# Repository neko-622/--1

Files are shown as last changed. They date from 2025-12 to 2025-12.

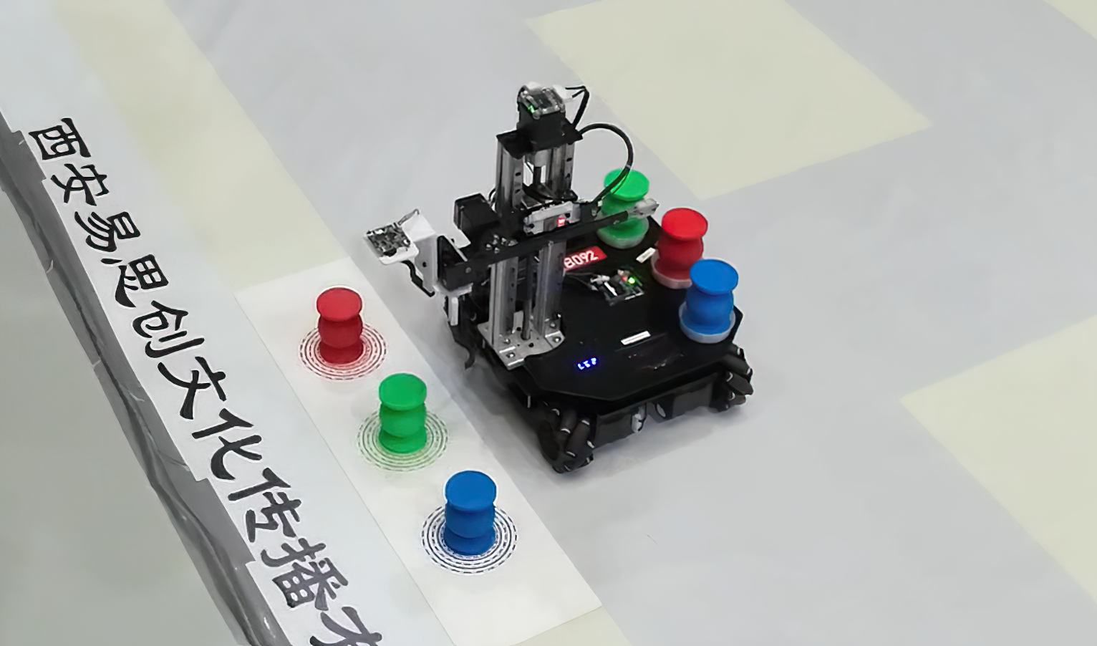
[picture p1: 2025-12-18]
2025智能物流项目简介_任务命题文档/IMG_8247.PNG

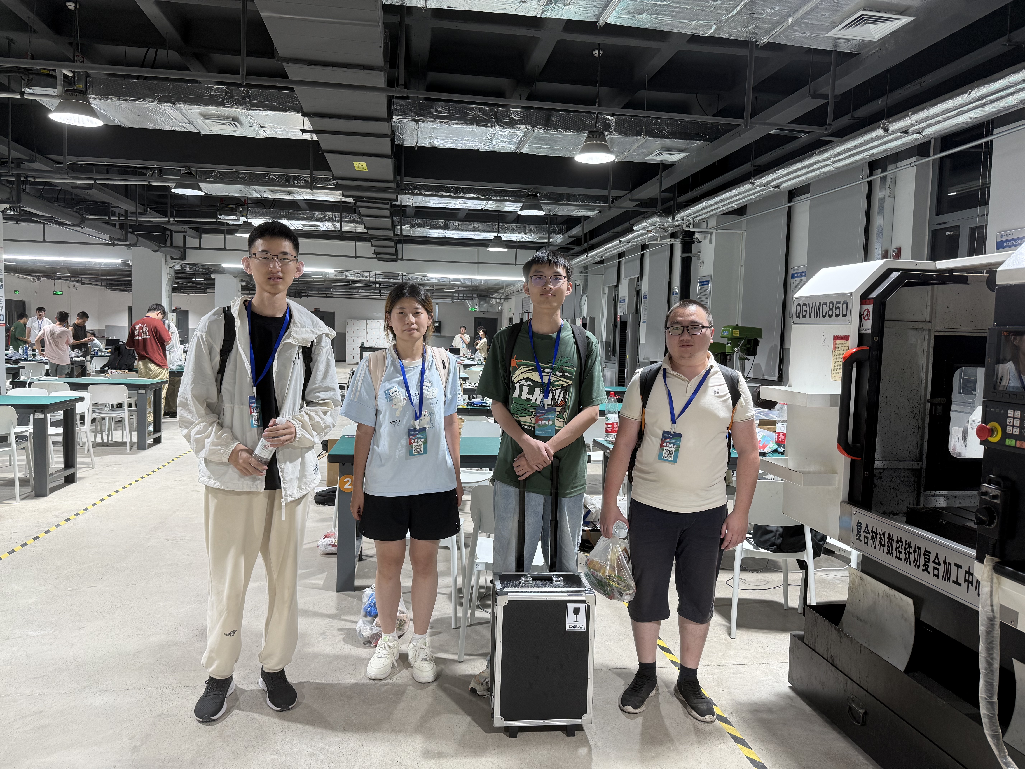
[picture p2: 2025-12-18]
2025智能物流项目简介_任务命题文档/IMG_8206.JPG

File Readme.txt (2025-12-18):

注意事项
1.PCB文件打板前请仔细检查所有封装，塔吊扩展板的降压模块可以自行替换。
2.视觉和电控代码都是经过实机测试的，不会有重大bug，但是注意电机模式和零位！
4.机械开源仅供参考，因为SW模型导出制图文件后又进行了少量的修改，整体没有大问题，但是细节需要自行打磨，打印件同理。
5.机械打板之前仔细检查孔位，可能有理线孔位置略有偏差，实物电机替换为DM4310，孔位和高度均不一致，根据实际需求修改。
6.机械打板推荐使用玻纤，因为绝缘。碳板导电。
7.注意硬件接线，注意电机零位，谨慎测试，注意安全！

2025年9月11日修改/勘误
1.共轴连接器购买链接错误，已经替换。

2025年9月18日提醒
1.PCB板中的降压模块由我们自行设计，封装如图箭头7，目前正在立创开源平台审核，我们自己是批量smt生产的，考虑到大家smt成本较高，建议大家使用其他商品降压模块进行替换，减小工作量且节约时间，后续将会上传替换降压模块的pcb版本。

2025年9月21日更新
1.前期提到的降压模块大家难以复刻的问题，已经上传修改了电源板和塔吊综合板降压模块的PCB文件。使用到的降压模块链接稍后更新到物料清单。再次提醒大家PCB打板之前细心检查，我们不对复刻过程中产生的任何损失负责。
2.在物料清单中更新了降压模块购买链接。
注意事项
1.电源板使用5V3A稳压输出模块，塔吊综合板的输出电压大家根据使用的舵机型号自定，模块输出电压可通过更换贴片电阻改变，详情询问客服。

2025年9月27日更新
1.整合了PCB文件，加入了
①降压模块
②新的2层主控板
③适配商品降压模块的电源板和塔吊综合板
2.在物料清单中更新了
①丝杆底部轴承型号
②原版低扭矩数字舵机（价格低但扭矩小）
③加入了铝型材购买时两端攻丝的提示

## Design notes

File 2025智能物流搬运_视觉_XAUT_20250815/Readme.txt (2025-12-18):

运行环境
开发板：Jetson Orin Nano 8GB
系统：SDK刷Jetson纯净系统（jetpack5.1.4）
环境：OpenCV

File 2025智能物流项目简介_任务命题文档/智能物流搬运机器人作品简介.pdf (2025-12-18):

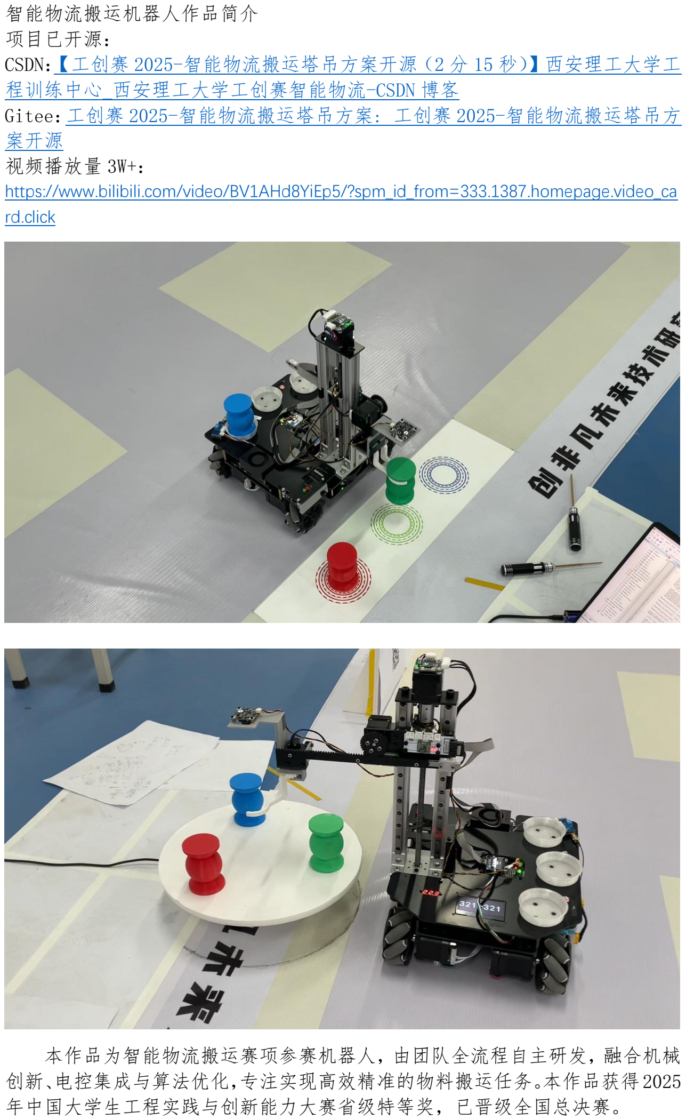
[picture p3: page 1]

智能物流搬运机器人作品简介
项目已开源：
CSDN：【工创赛 2025-智能物流搬运塔吊方案开源（2 分 15 秒）】西安理工大学工 程训练中心_西安理工大学工创赛智能物流-CSDN 博客 (https://blog.csdn.net/m0_74056439/article/details/150104661?spm=1001.2014.3001.5502)
Gitee：工创赛 2025-智能物流搬运塔吊方案: 工创赛 2025-智能物流搬运塔吊方 案开源 (https://gitee.com/pinksakura/Logistics_Vehicle_F407_V2)
视频播放量 3W+：
https://www.bilibili.com/video/BV1AHd8YiEp5/?spm_id_from=333.1387.homepage.video_ca rd.click (https://www.bilibili.com/video/BV1AHd8YiEp5/?spm_id_from=333.1387.homepage.video_card.click)

本作品为智能物流搬运赛项参赛机器人，由团队全流程自主研发，融合机械 创新、电控集成与算法优化，专注实现高效精准的物料搬运任务。本作品获得2025 年中国大学生工程实践与创新能力大赛省级特等奖，已晋级全国总决赛。

一、全自主设计与技术创新
整车机械、电控、视觉及硬件均自主开发，核心 PCB（主控 / 电源 / 拓展 / 塔吊转接）自主绘制打样，保障硬件系统的高集成与可靠性。机械 结构创新性采用 “塔吊”设计，灵活性大大提高。
搭载双重算法：视觉算法通过抗干扰优化，在强光干扰或目标部分遮挡 的情况下仍然可以准确识别目标；底盘定位结合麦克纳姆轮逆运动学解算， 配合视觉校正算法，实现 ±2mm 级精度，可精确按照预定轨迹运动，并无 误差返回出发点。
二、任务效率与功能突破
通过全流程时序优化，平均完赛时间控制在 2 分 15 秒内。支持 “一 键式” 自主运行，具备定位、二维码读取、多色物料跟踪抓取及色环 1 环 精度码垛等功能。
能源系统采用自主设计的锂电池组，满足全程能耗需求，支持实时电压 监测，支持电池热替换。
三、场景适配与工程价值
作品高集成、高稳定的特点，既满足赛事技术要求，也贴近智能制造对 物流自动化的实际需求，展现从实验室到工业应用的转化潜力。 团队以 “自主创新 + 工程落地” 为目标，通过全自主设计制作，以 敢于直面困难的精神，在赛事中呈现当代大学生的创新素养。

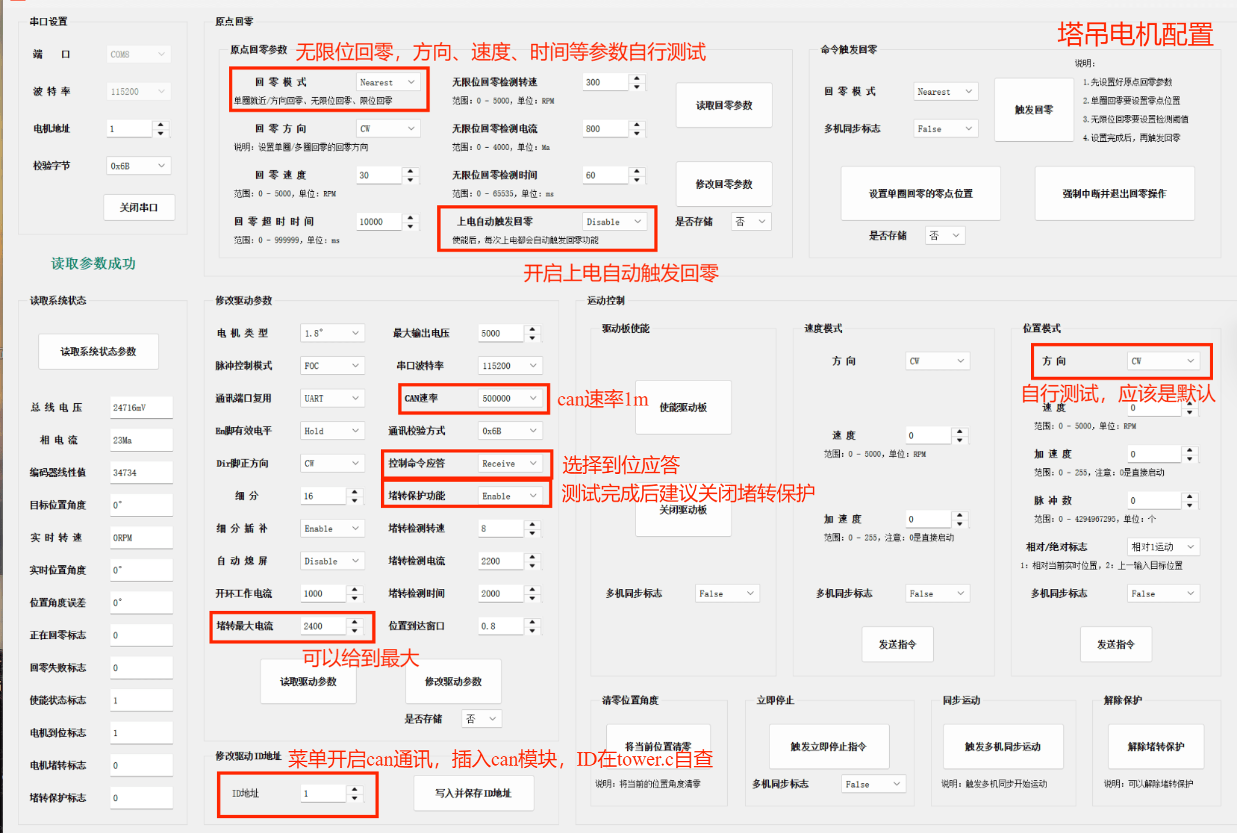
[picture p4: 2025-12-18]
附加资料及参数/塔吊张大头参数.png

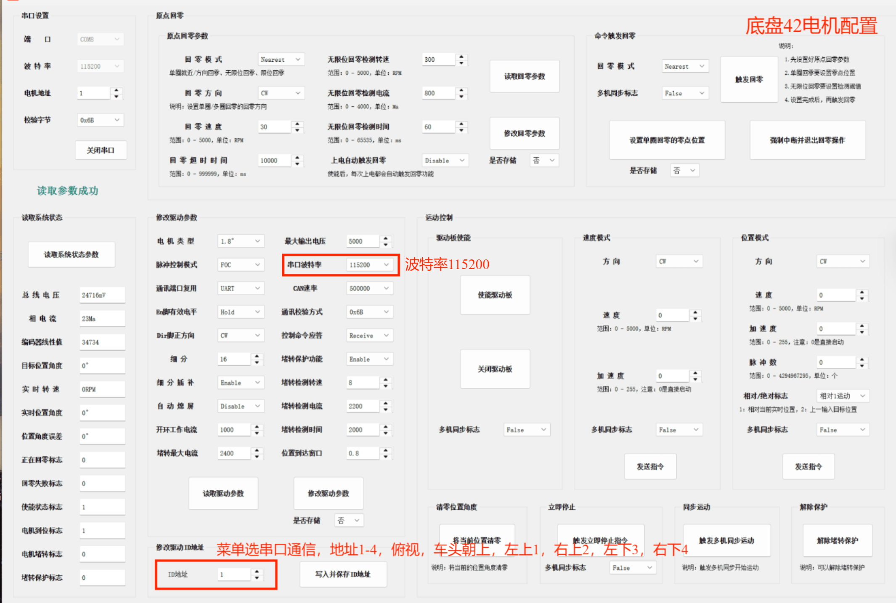
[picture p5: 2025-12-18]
附加资料及参数/底盘张大头参数.png

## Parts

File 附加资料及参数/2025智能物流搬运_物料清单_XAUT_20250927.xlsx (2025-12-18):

2025智能物流搬运_物料清单_XAUT_20250927
请注意，本清单中不包含所需要的基本工具。
名称 | 选型 | 数量 | 备注 | 单价（仅供参考） | 链接
Jeston Orin Nano | 官方版 开发套件 | 1 |  | 2469 | NVIDIA英伟达JETSON Orin Nano Super开发板官方套件AI核心模组NX-tmall.com天猫 (https://detail.tmall.com/item.htm?ali_trackid=1_ffb2a0857a5ef13fcd62ed45b887f8ad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)
OPS-9平面定位系统 |  | 1 |  | 3680 | OPS-9平面定位系统 陀螺仪编码器 机器人Robocon2018-淘宝网 (https://item.taobao.com/item.htm?id=524772631462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)
轮趣C100摄像头 | 新版C100带金属外壳超大FOV相机 | 1 | 识别摄像头 | 137.3 | RGB相机C100金属外壳高清C70大FOV适Ubuntu系统1080P摄像头RDK X5-tmall.com天猫 (https://detail.tmall.com/item.htm?id=756772432605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)
花雀200万像素摄像头 | 广角130度 | 1 | 扫码摄像头 | 28.8 | 200万像素1080PHD 笔记本电脑一体机广告机3D打印机USB摄像头模组-淘宝网 (https://item.taobao.com/item.htm?abbucket=0&id=846689762617&ns=1&xxc=taobaoSearch)
张大头Emm42 | Emm42_V5.0 PLC套餐 带42-40磁柱电机 | 4 | 底盘电机 | 69.99 | 42步进闭环电机3d打印机控制器A4988替换TMC2209超静音驱动模块-淘宝网 (https://item.taobao.com/item.htm?id=673302946671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)
达妙DM4310 | 电机（含驱动）+USB转CAN模块 | 1 | 塔吊Yaw电机 | 648 | MIT驱动无刷伺服械臂机器人达妙科技关节电机FOCGM43减速双编码器-淘宝网 (https://item.taobao.com/item.htm?id=815333472865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)
张大头X35 | ZDT_X35_V2.0-CAN套餐 | 1 | 塔吊升降电机驱动板 | 56.99 | 42步进闭环电机3d打印机控制器替换A4988/TMC2209超静音驱动模块-淘宝网 (https://item.taobao.com/item.htm?id=723766480162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)
张大头X28 | ZDT_X28_V2.0-CAN套餐 | 1 | 塔吊伸缩电机驱动板 | 56.99 | 42步进闭环电机3d打印机控制器替换A4988/TMC2209超静音驱动模块-淘宝网 (https://item.taobao.com/item.htm?id=723766480162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)
张大头35步进 | 35电机-带磁柱孔 机身35mm长 | 1 | 塔吊升降电机 | 33.99 | 35步进电机带磁柱孔马达两相四线雕刻机写字机闭环加装3D打印配件-淘宝网 (https://item.taobao.com/item.htm?id=723690490192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)
张大头28步进 | 28电机-带磁柱孔 机身32mm长 | 1 | 塔吊伸缩电机 | 35.99 | 28步进电机带磁柱孔马达两相四线雕刻机写字机闭环加装3D打印配件-淘宝网 (https://item.taobao.com/item.htm?id=742293686973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)
幻尔数字舵机LFD-01M | LFD-01M数字舵机+金属舵盘 | 1 | 夹爪舵机（可升级为下款） | 43.1 | 幻尔 数字舵机 微型防堵转LFD-01M金属轴9克机器人机械臂智能小车-tmall.com天猫 (https://detail.tmall.com/item.htm?id=607882018620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)
麦克纳姆轮 | 黑色-80mm-5mm铝轴 | 1 |  | 118 | 竞赛级麦克纳姆轮 专业ROS机器人智能小车底盘轮子万向轮AGV-淘宝网 (https://item.taobao.com/item.htm?id=609745520995&sku_properties=-1%3A-8)
2.42OLED屏幕 | 白色-不焊针 | 1 | 任务码显示 | 48 | 黄保凯中景园2.42寸12864 OLED显示屏12864液晶屏2.4寸oledsd1309-淘宝网 (https://item.taobao.com/item.htm?_u=1201gv8icp06eb&id=560794215430)
0.96OLED屏幕 | 0.96寸7管脚白色 不焊排针 | 1 | 系统信息显示 | 13 | 0.96寸OLED显示屏模块0.91 1.3 1.54寸12864液晶屏4/6/7针IIC/SPI-tmall.com天猫 (https://detail.tmall.com/item.htm?_u=1201gv8icpbfed&id=617450807815)
隔离电源 | 40W-24V(18-36V)-12V | 1 | 工控机供电 | 89 | DCDC隔离电源模块稳压24V转5V12V24V降压模块5W6W现货WD5-24S05A1-淘宝网 (https://item.taobao.com/item.htm?abbucket=0&id=24076196021&ns=1&skuId=4867188199590&xxc=taobaoSearch)
数字电压表 | 二线0.28寸 4.2-30V 蓝色 | 1 | 电池电压显示 | 6.9 | Zave 0.28/0.36英寸数字电压表头30/100V数码管微型数显两二/三线-tmall.com天猫 (https://detail.tmall.com/item.htm?_u=1201gv8icpd61a&id=609651741222)
金属按钮开关 | 8mm白色自锁 | 1 | 电源开关 | 6.5 | 8mm 10mm金属按钮开关自复自锁电源带灯常开焊脚防水启动按键开关-tmall.com天猫 (https://detail.tmall.com/item.htm?_u=1201gv8icp84a7&id=631243953978)
金属按钮开关 | 8mm无灯自复 | 1 | 一键启动 | 4.5 | 8mm 10mm金属按钮开关自复自锁电源带灯常开焊脚防水启动按键开关-tmall.com天猫 (https://detail.tmall.com/item.htm?_u=1201gv8icp84a7&id=631243953978)
DC-DC降压电源模块 | DC-DC降压模块5V/3A | 2 | 降压模块 | 3.2 | DC-DC降压电源模块 5V-30V输入转3.3V/5V输出 3A迷你降压车载电源-淘宝网 (https://item.taobao.com/item.htm?id=644346322045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)
XH2.54连接线、GH1.25连接线均购于该店铺，请自行选型。 |  |  |  |  | 首页-莫斯电子-淘宝网 (https://shop58274919.taobao.com/?spm=pc_detail.30350276.shop_block.dshopinfo.69af7dd6oGgVc1)
丝杆和丝母 | 导程8-250mm配螺母 | 1 |  | 7 | 3D打印机丝杆T型丝杆T8丝杆步进电机丝杆梯形丝杆T型螺母-淘宝网 (https://item.taobao.com/item.htm?_u=1201gv8icpc378&id=674124727609)
丝母座 | T8螺母座老款 | 1 |  | 8 | T8 T10 T12 T16 T20 螺母转换座 四方转换块丝杆配件 铜螺母座子-淘宝网 (https://item.taobao.com/item.htm?id=541780928313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)
联轴器 | 外径20长度25孔径5*8 | 1 |  | 4.3 | 刚性联轴器铝合金20*25外径20长度25 5*8*8*10连轴器步进电机钢性-tmall.com天猫 (https://detail.tmall.com/item.htm?id=627174806360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)
2020铝型材 |  | 2 | 两端需要攻丝，下单后告知商家
2020角码 |  | 4
MGN7滑轨 |  | 1
MGN9滑轨 |  | 2
轴承 | 外径12内径8厚3.5 | 1 | 丝杆底部轴承 | 2 | 轴承微小型高速迷你型号大全内径1 2 3 4 5 6 7 8 9 10 12mm精密-淘宝网 (https://item.taobao.com/item.htm?from=cart&id=926515029231&skuId=5807980453867&upStreamPrice=200)
铝排 |  | 若干 | 板材连接件 | 1.5 | 【组团加工】四面M3铝排连接件50件起发货 方管 各种CNC数控加工-淘宝网 (https://item.taobao.com/item.htm?id=654402789442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)
底盘共轴连接器 |  | 1 | 底盘摆式悬挂 | 60 | 天府之土麦克纳姆 轮小车底盘机器人底盘共轴双板连接器智能车-淘宝网 (https://item.taobao.com/item.htm?app=chrome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)
以下材料选配
HDMI屏幕（选配） | 无触摸 | 1 | 显示工控机状态 | 105 | 3.5寸树莓派显示器HDMI接口电阻触摸电脑扩展屏320*480支持AIDA64-淘宝网 (https://item.taobao.com/item.htm?_u=1201gv8icp0c9e&id=740631123830&skuId=5276986098031)
HDMI线（选配） | 标准DP直头+HDMI上弯+15/20cm排线 | N/A | 视频信号传输 | N/A | DP转HDMI软排线90度弯头电脑显示器高清视频航拍摄影转接器连接线-tmall.com天猫 (https://detail.tmall.com/item.htm?_u=1201gv8icp6f9a&id=732598235744)
幻尔高速空心杯数字舵机 | HPS-0618SG数字舵机+金属舵盘 | 1 | 夹爪舵机（高扭矩，使用需要调整孔位） | 163 | 幻尔高速空心杯数字舵机HPS-0618SG机器人机器狗180度PWM微型舵机-tmall.com天猫 (https://detail.tmall.com/item.htm?id=667689779519&skuId=5699590755734)

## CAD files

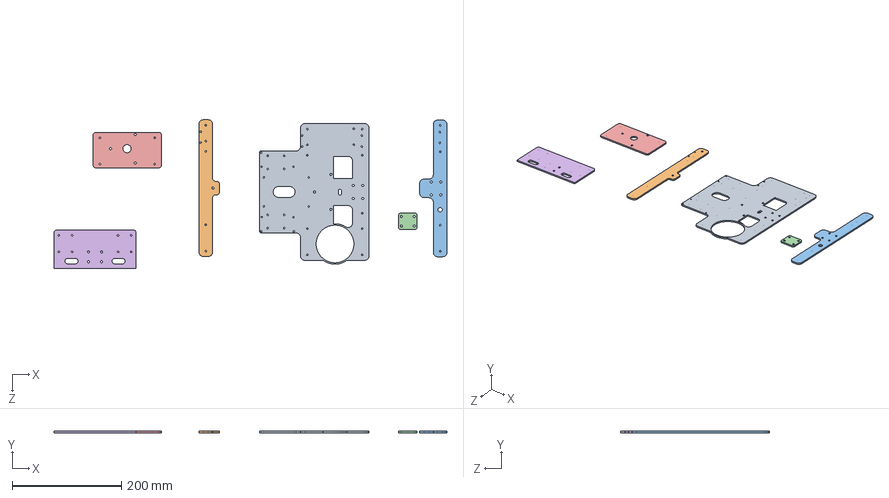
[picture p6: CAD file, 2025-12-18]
2025智能物流搬运_机械_XAUT_20250811/板件/装配体1.SLDASM
718.0 x 3.00 x 271.5 mm
25物流车测试底盘-底盘-板件-底板后
25物流车测试底盘-底盘-板件-后加强筋板
25物流车测试底盘-底盘-板件-前加强筋
25物流车测试底盘-底盘-板件-前悬挂垫片
25物流车测试底盘-底盘-板件-塔吊底板
25物流车1.0-底盘-碳板-3mm-底板前

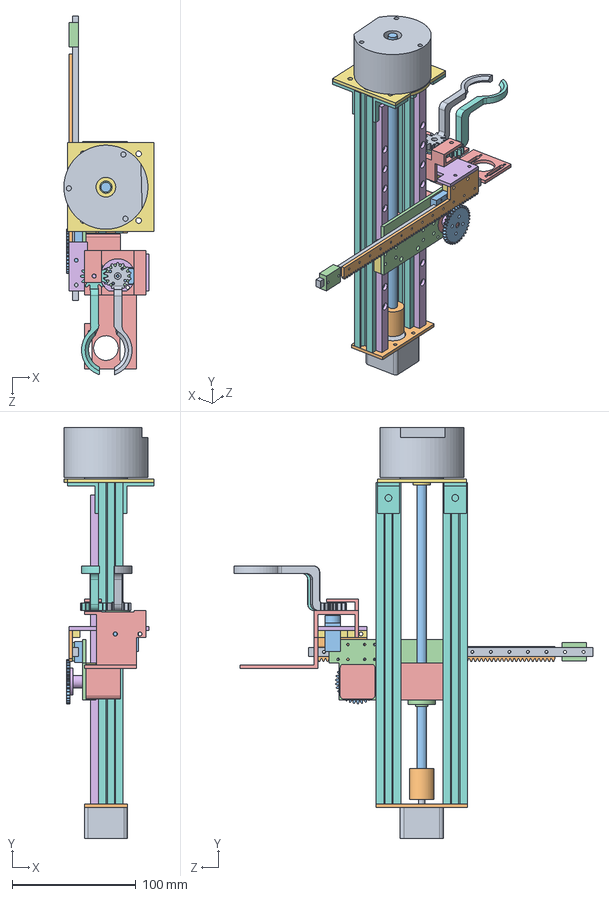
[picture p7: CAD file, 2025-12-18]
2025智能物流搬运_机械_XAUT_20250811/抓取机构/25物流车1.0-抓取机构-升降模块装配.SLDASM
73.0 x 332.5 x 290.2 mm
25物流车1.0-抓取机构-电子-标准件-35闭环步进电机
25物流车1.0-抓取机构-标准件-刚性联轴器-5-8
25物流车1.0-抓取机构-标准件-丝杆-8-200
25物流车1.0-抓取机构-标准件-丝母-M8
25物流车1.0-抓取机构-标准件-丝母座-M8
25物流车1.0-抓取机构-标准件-滑轨-MGN9C x 2
25物流车1.0-抓取机构-标准件-滑块-MGN9C x 2
25物流车1.0-抓取机构-铝型材-2020-217 x 2
25物流车1.0-抓取机构-电子-标准件-g6220
25物流车1.0-抓取机构-碳板-3mm-升降35电机固定板
25物流车1.0-抓取机构-碳板-3mm-圆柱齿轮
25物流车1.0-抓取机构-碳板-3mm-水平轴连接板
25物流车1.0-抓取机构-电子-标准件-28闭环步进电机
25物流车1.0-抓取机构-标准件-法兰联轴器-5mm
25物流车1.0-抓取机构-cnc-yaw轴转接
25物流车1.0-抓取机构-铝型材-2020-2孔角件 x 4
25物流车1.0-抓取机构-标准件-滑轨-MGN7C
25物流车1.0-抓取机构-碳板-3mm-齿条3
25物流车1.0-标准件-电子-mg90
25物流车1.0-抓取机构-标准件-mg90舵盘
25物流车1.0-抓取机构-打印-舵机支架3
25物流车1.0-抓取机构-碳板-3mm-夹爪连板
25物流车1.0-抓取机构-标准件-板材连接件 x 3
25物流车1.0-抓取机构-打印-夹爪左
25物流车1.0-抓取机构-打印-夹爪右
25物流车1.0-抓取机构-标准件-轴套3-5-3.6 x 2
25物流车1.0-抓取机构-标准件-滑块-MGN7C x 2
25物流车测试底盘-打印-限位块

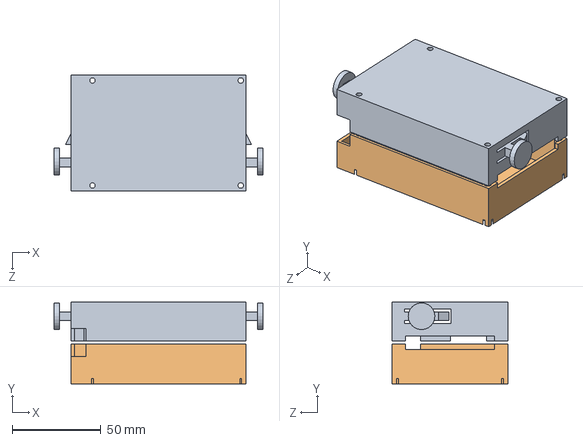
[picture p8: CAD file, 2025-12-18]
2025智能物流搬运_机械_XAUT_20250811/打印/25物流车测试地盘底盘-打印-电池外壳装配.SLDASM
117.5 x 46.1 x 65.0 mm
25物流车测试底盘-打印-电池盒上盖
25物流车测试底盘-打印-电池盒下盖

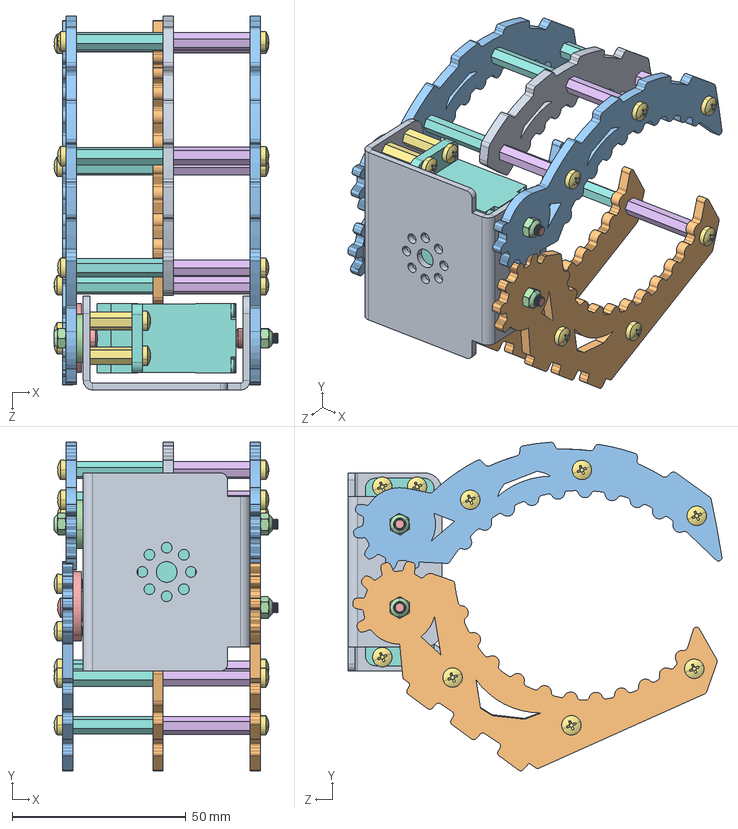
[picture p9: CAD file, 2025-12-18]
2025智能物流搬运_机械_XAUT_20250811/抓取机构/25物流车1.0-抓取机构-金属大爪子1.SLDASM
64.4 x 94.5 x 107.6 mm
________.STEP
____1.STEP
____2.STEP x 2
________M3.STEP x 3
cross recessed pan head screws gb_GB_CROSS_SCREWS_TYPE1 M3X10-10 H type-S.STEP x 6
cross recessed ctsk head tapping screws gb_GB_CROSS_SCREWS_TYPE129 ST2.9X6.5 H C-S.STEP x 4
____M3_12.STEP x 4
________-0.STEP
____22.STEP
____11.STEP
____3.STEP
____.STEP
__________.STEP
____M3_25.STEP x 6
cross recessed pan head screws gb_GB_CROSS_SCREWS_TYPE1 M3X6-6 H type-S.STEP x 18
________M3_25.STEP x 6

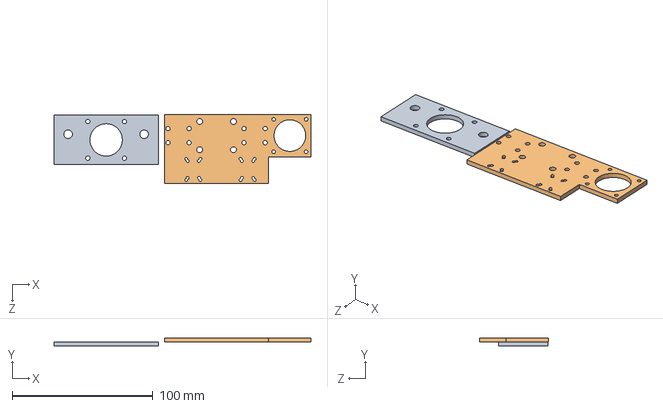
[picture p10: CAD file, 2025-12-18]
2025智能物流搬运_机械_XAUT_20250811/抓取机构/3-1.SLDASM
182.4 x 6.00 x 49.0 mm
25物流车1.0-抓取机构-碳板-3mm-升降35电机固定板
25物流车1.0-抓取机构-碳板-3mm-水平轴连接板

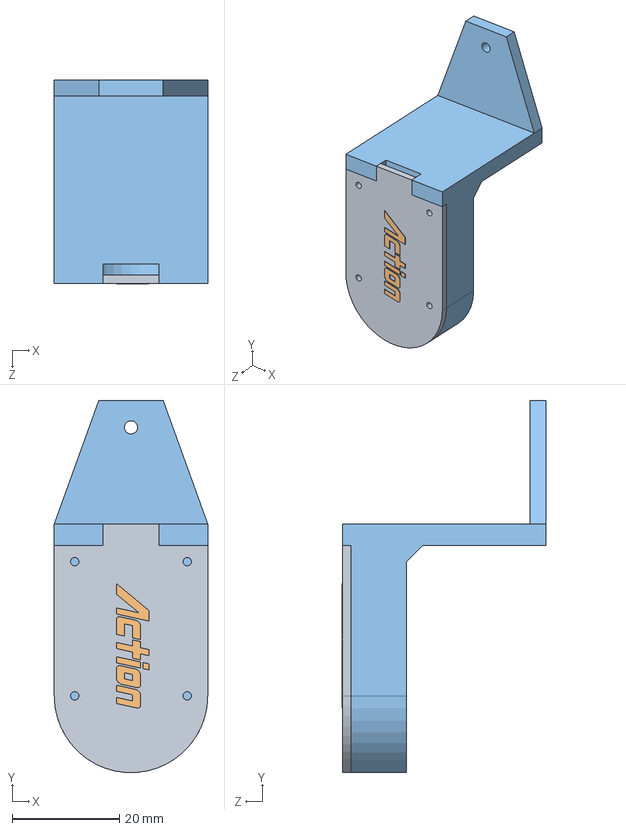
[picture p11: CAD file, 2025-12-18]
2025智能物流搬运_机械_XAUT_20250811/定位系统三维图/三维/编码器电路板改.SLDASM
28.6 x 69.3 x 38.0 mm
编码器电路板改
ACTION
弯折改

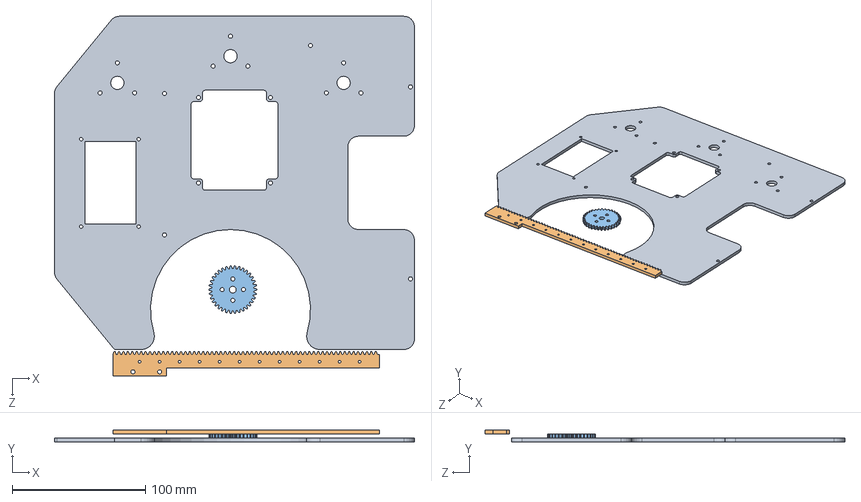
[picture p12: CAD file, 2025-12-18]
2025智能物流搬运_机械_XAUT_20250811/板件/玻纤3.SLDASM
270.0 x 9.00 x 269.7 mm
25物流车测试底盘-底盘-板件-上板
25物流车1.0-抓取机构-碳板-3mm-齿条3
25物流车1.0-抓取机构-碳板-3mm-圆柱齿轮

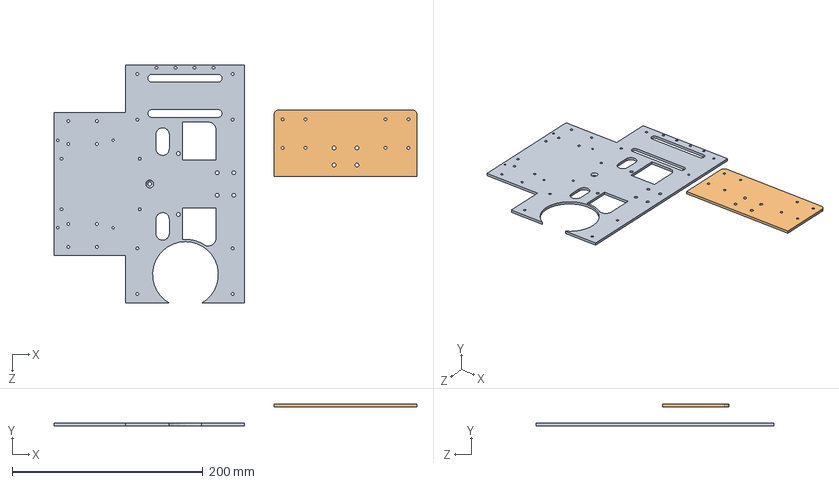
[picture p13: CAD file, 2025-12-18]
2025智能物流搬运_机械_XAUT_20250811/板件/测试3.SLDASM
381.0 x 23.0 x 250.0 mm
25物流车测试底盘-底盘-板件-底板后
25物流车1.0-底盘-碳板-3mm-底板前

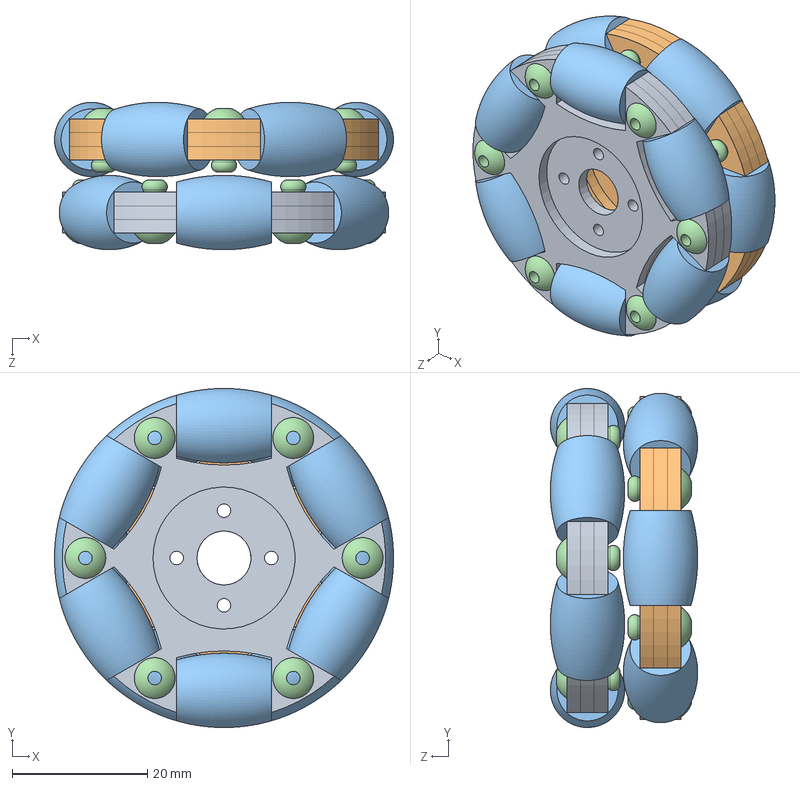
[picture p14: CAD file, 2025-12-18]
2025智能物流搬运_机械_XAUT_20250811/定位系统三维图/三维/2mm全向轮.SLDASM
50.1 x 50.1 x 21.8 mm
2mm全向轮片2
2mm全向轮片1
从动 x 12
铆钉 x 12

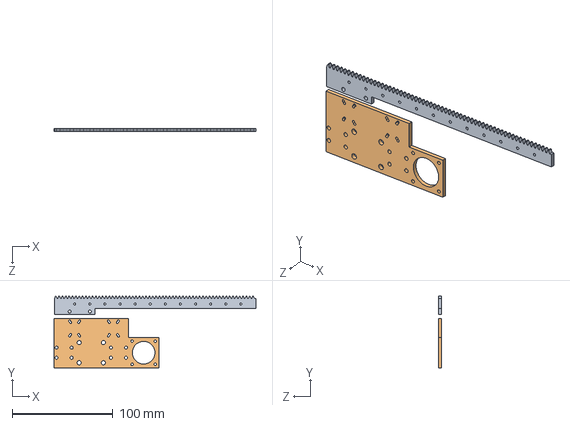
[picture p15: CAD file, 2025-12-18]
2025智能物流搬运_机械_XAUT_20250811/抓取机构/板件/装配体2.SLDASM
200.5 x 71.1 x 3.00 mm
25物流车1.0-抓取机构-碳板-3mm-齿条3
25物流车1.0-抓取机构-碳板-3mm-水平轴连接板

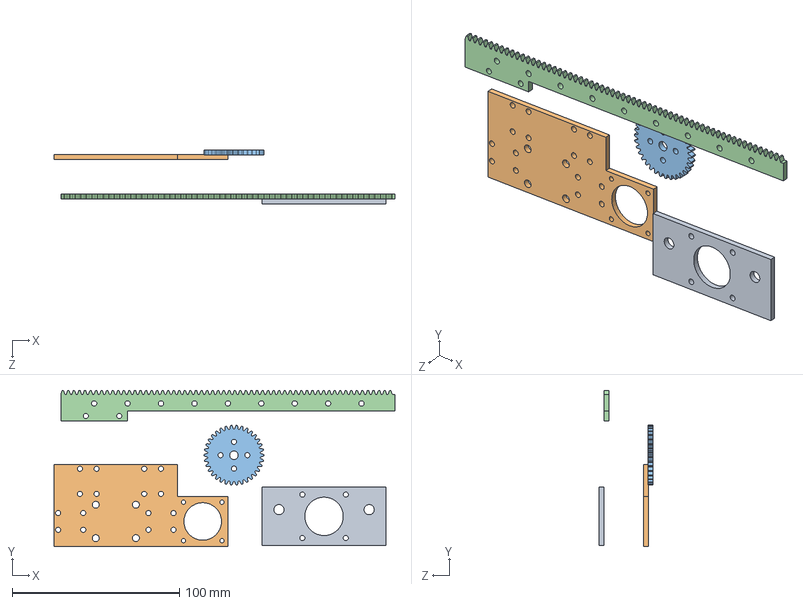
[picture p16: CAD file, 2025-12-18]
2025智能物流搬运_机械_XAUT_20250811/抓取机构/板件/3.SLDASM
204.1 x 93.4 x 32.5 mm
25物流车1.0-抓取机构-碳板-3mm-升降35电机固定板
25物流车1.0-抓取机构-碳板-3mm-水平轴连接板
25物流车1.0-抓取机构-碳板-3mm-圆柱齿轮
25物流车1.0-抓取机构-碳板-3mm-齿条3

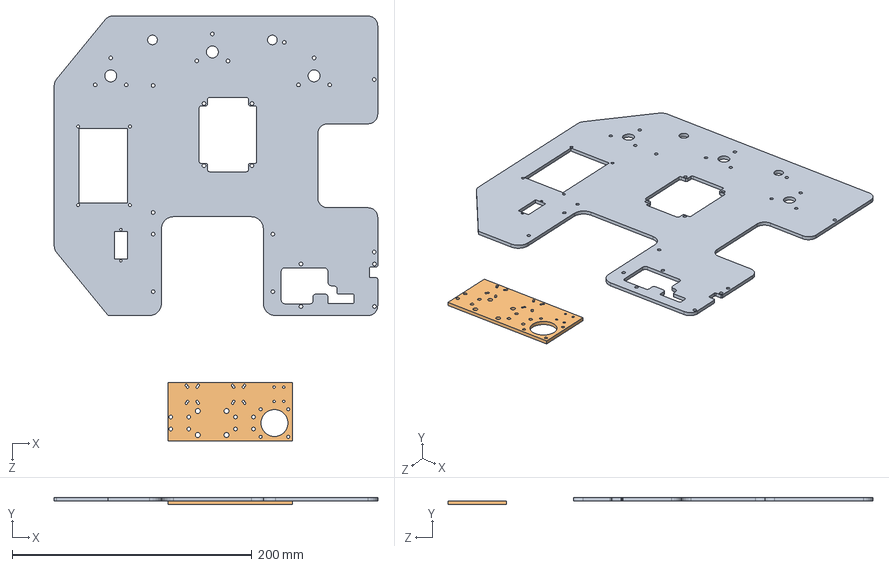
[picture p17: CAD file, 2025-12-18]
2025智能物流搬运_机械_XAUT_20250811/板件/33.SLDASM
270.0 x 6.00 x 354.7 mm
25物流车测试底盘-底盘-板件-上板
25物流车1.0-抓取机构-碳板-3mm-水平轴连接板

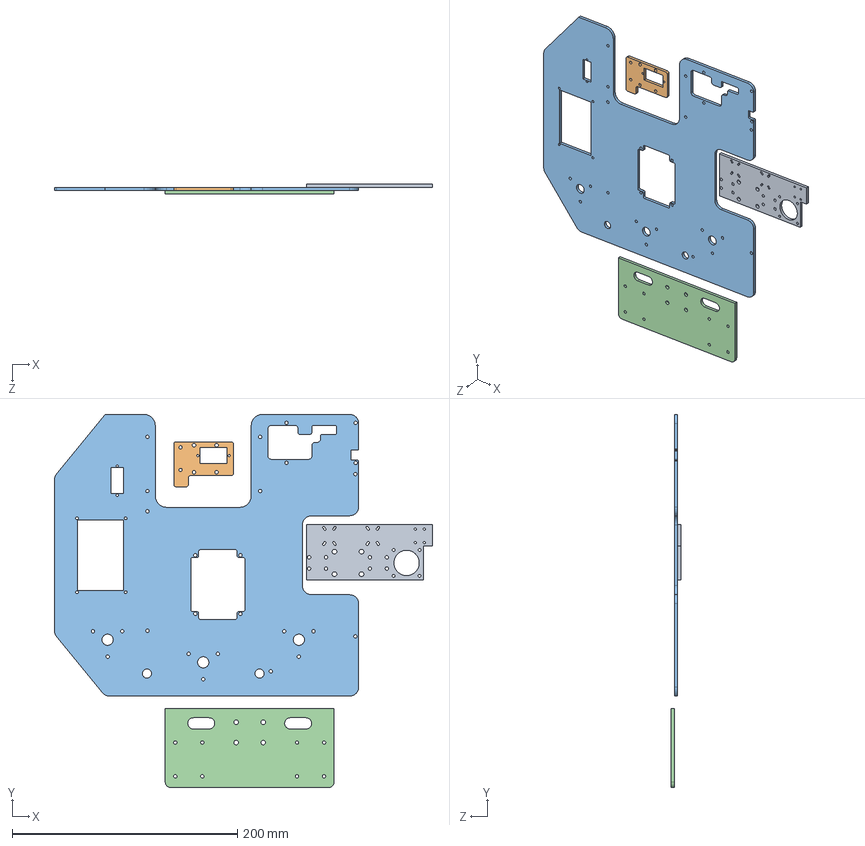
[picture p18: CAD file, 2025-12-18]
2025智能物流搬运_机械_XAUT_20250811/抓取机构/板件/333.SLDASM
335.5 x 331.2 x 9.00 mm
25物流车1.0-抓取机构-碳板-3mm-水平轴连接板
25物流车1.0-抓取机构-碳板-3mm-mg90夹爪连板
25物流车测试底盘-底盘-板件-上板
25物流车1.0-底盘-碳板-3mm-底板前

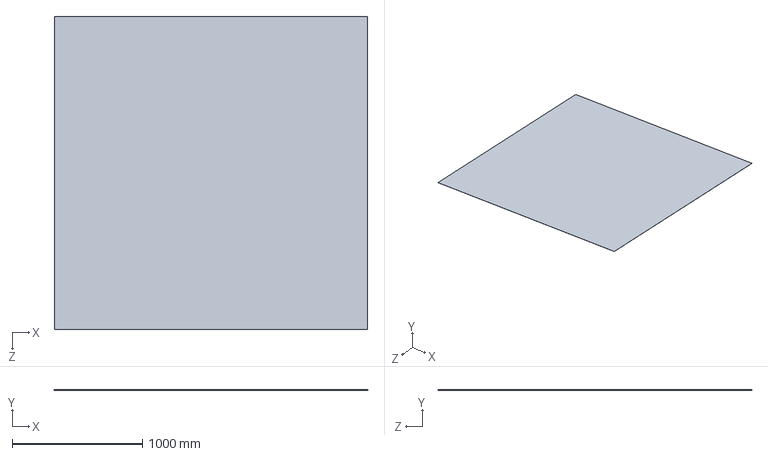
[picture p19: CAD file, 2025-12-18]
2025智能物流搬运_机械_XAUT_20250811/2025-场地.SLDPRT
2400.0 x 1.00 x 2400.0 mm

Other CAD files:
2025智能物流搬运_机械_XAUT_20250811/五金/25物流车测试底盘-底盘-标准件-42步进电机支架.SLDPRT
2025智能物流搬运_机械_XAUT_20250811/定位系统三维图/三维/导轨固定.SLDPRT
2025智能物流搬运_机械_XAUT_20250811/打印/25物流车测试底盘-打印-电池支架垫片.SLDPRT
2025智能物流搬运_机械_XAUT_20250811/抓取机构/3-2.DWG
2025智能物流搬运_机械_XAUT_20250811/2025-物料.SLDPRT
2025智能物流搬运_机械_XAUT_20250811/25物流车测试底盘-底盘-松木地板.SLDPRT
2025智能物流搬运_机械_XAUT_20250811/25物流车测试底盘-底盘-板件-上板.step.SLDPRT
2025智能物流搬运_机械_XAUT_20250811/25物流车测试底盘-物料架.SLDPRT
2025智能物流搬运_机械_XAUT_20250811/25物流车测试底盘-物料架.STL
2025智能物流搬运_机械_XAUT_20250811/25物流车测试底盘-物料盘.SLDPRT
2025智能物流搬运_机械_XAUT_20250811/25物流车测试底盘-物料盘联轴器.SLDPRT
2025智能物流搬运_机械_XAUT_20250811/25物流车测试底盘-物料盘联轴器.STL
2025智能物流搬运_机械_XAUT_20250811/五金/25物流车测试底盘-底盘-标准件-42步进电机支架.STL
2025智能物流搬运_机械_XAUT_20250811/五金/25物流车测试底盘-底盘-标准件-75mm直径麦轮.SLDPRT
2025智能物流搬运_机械_XAUT_20250811/五金/25物流车测试底盘-底盘-标准件-小交滚轴承.SLDPRT
2025智能物流搬运_机械_XAUT_20250811/五金/25物流车测试底盘-底盘-标准件-底盘悬挂.SLDPRT
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

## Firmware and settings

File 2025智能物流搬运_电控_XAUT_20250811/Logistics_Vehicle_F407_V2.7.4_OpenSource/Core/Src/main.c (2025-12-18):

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
/* Includes ------------------------------------------------------------------*/
#include "main.h"
#include "cmsis_os.h"
#include "can.h"
#include "dma.h"
#include "i2c.h"
#include "spi.h"
#include "tim.h"
#include "usart.h"
#include "gpio.h"


/* USER CODE BEGIN PV */
struct RC_DATA RC_RX;
uint8_t color_task[6]={0};

int circle_x[3]={880,1025,1160};  //红 绿 蓝
int circle_y[3]={1150,990,840};   //红 绿 蓝
struct VISUAL_DATA VIS_RX;  //视觉接收数据

int SpeedTarget[4]={0};

float pos_x=0;
float pos_y=0;
float zangle=0;
float xangle=0;
float yangle=0;
float w_z=0;

/* 先定义好存放数据的空间，队列大小是5，这里就定义5个。 */
UART2_RX_TypeDef uart2_rx_data_t[UART_BUFFER_QUANTITY];
UART5_RX_TypeDef uart5_rx_data_t[UART_BUFFER_QUANTITY];
UART1_RX_TypeDef uart1_rx_data_t[UART_BUFFER_QUANTITY];
/* 定义一个变量用作分配上面定义的数据 */
uint8_t uart2_buff_ctrl = 0;
uint8_t uart5_buff_ctrl = 0;
uint8_t uart1_buff_ctrl = 0;
/* 引用串口DMA handle  */
extern DMA_HandleTypeDef hdma_usart2_rx;
extern DMA_HandleTypeDef hdma_uart5_rx;
extern DMA_HandleTypeDef hdma_usart1_rx;
/* 队列 handle。去freertos.c文件里面找CubeMX给你创建好的。 */
extern osMessageQId uart2_queueHandle;
extern osMessageQId uart5_queueHandle;
extern osMessageQId uart1_queueHandle;

/* USER CODE END PV */

void SystemClock_Config(void);
void MX_FREERTOS_Init(void);
/* USER CODE BEGIN 0 */
/* Redirect printf function */
int fputc(int ch, FILE *f)
{
    HAL_UART_Transmit(&huart2, (uint8_t *)&ch, 1, 1000);
    return (ch);
}
 
void USART2_DMAHandler(void)
{
    if (RESET != __HAL_UART_GET_FLAG(&huart2, UART_FLAG_IDLE)) // 判断是否是空闲中断
    {
        UART2_RX_TypeDef *pUart2Data; /* 定义指向创建串口数据的指针 */
 
        __HAL_UART_CLEAR_IDLEFLAG(&huart2); // 清除空闲中断标志
        HAL_UART_DMAStop(&huart2);          // 停止本次DMA传输
 
        /* 计算接收到的数据长度，放进串口数据结构体中 */
        uart2_rx_data_t[uart2_buff_ctrl].size = UART2_BUFFER_SIZE - __HAL_DMA_GET_COUNTER(&hdma_usart2_rx);
        /* 将这个串口数据的结构体地址给指针 */
        pUart2Data = &uart2_rx_data_t[uart2_buff_ctrl];
        /* 把指向串口接收数据的指针放入消息队列。注意，这里传的是指针的地址，也就是指针串口数据结构体的指针的地址不能传pUartData本身 */
        xQueueSendFromISR(uart2_queueHandle, &pUart2Data, NULL);
        /* 这里进行加一，使其下一次DMA传输时将接收的数据放到下一个串口缓冲区中 */
        uart2_buff_ctrl++;
        /* 取余操作防止越界 */
        uart2_buff_ctrl %= UART_BUFFER_QUANTITY;
        /* 重启开始DMA传输 */
        HAL_UART_Receive_DMA(&huart2, uart2_rx_data_t[uart2_buff_ctrl].buffer, UART2_BUFFER_SIZE);
    }
}

void USART5_DMAHandler(void)
{
    if (RESET != __HAL_UART_GET_FLAG(&huart5, UART_FLAG_IDLE)) // 判断是否是空闲中断
    {
        UART5_RX_TypeDef *pUart5Data; /* 定义指向创建串口数据的指针 */
 
        __HAL_UART_CLEAR_IDLEFLAG(&huart5); // 清除空闲中断标志
        HAL_UART_DMAStop(&huart5);          // 停止本次DMA传输
 
        /* 计算接收到的数据长度，放进串口数据结构体中 */
        uart5_rx_data_t[uart5_buff_ctrl].size = UART5_BUFFER_SIZE - __HAL_DMA_GET_COUNTER(&hdma_uart5_rx);
        /* 将这个串口数据的结构体地址给指针 */
        pUart5Data = &uart5_rx_data_t[uart5_buff_ctrl];
        /* 把指向串口接收数据的指针放入消息队列。注意，这里传的是指针的地址，也就是指针串口数据结构体的指针的地址不能传pUartData本身 */
        xQueueSendFromISR(uart5_queueHandle, &pUart5Data, NULL);
        /* 这里进行加一，使其下一次DMA传输时将接收的数据放到下一个串口缓冲区中 */
        uart5_buff_ctrl++;
        /* 取余操作防止越界 */
        uart5_buff_ctrl %= UART_BUFFER_QUANTITY;
        /* 重启开始DMA传输 */
        HAL_UART_Receive_DMA(&huart5, uart5_rx_data_t[uart5_buff_ctrl].buffer, UART5_BUFFER_SIZE);
    }
}

void USART1_DMAHandler(void)
{
    if (RESET != __HAL_UART_GET_FLAG(&huart1, UART_FLAG_IDLE)) // 判断是否是空闲中断
    {
        UART1_RX_TypeDef *pUart1Data; /* 定义指向创建串口数据的指针 */
 
        __HAL_UART_CLEAR_IDLEFLAG(&huart1); // 清除空闲中断标志
        HAL_UART_DMAStop(&huart1);          // 停止本次DMA传输
 
        /* 计算接收到的数据长度，放进串口数据结构体中 */
        uart1_rx_data_t[uart1_buff_ctrl].size = UART1_BUFFER_SIZE - __HAL_DMA_GET_COUNTER(&hdma_usart1_rx);
        /* 将这个串口数据的结构体地址给指针 */
        pUart1Data = &uart1_rx_data_t[uart1_buff_ctrl];
        /* 把指向串口接收数据的指针放入消息队列。注意，这里传的是指针的地址，也就是指针串口数据结构体的指针的地址不能传pUartData本身 */
        xQueueSendFromISR(uart1_queueHandle, &pUart1Data, NULL);
        /* 这里进行加一，使其下一次DMA传输时将接收的数据放到下一个串口缓冲区中 */
        uart1_buff_ctrl++;
        /* 取余操作防止越界 */
        uart1_buff_ctrl %= UART_BUFFER_QUANTITY;
        /* 重启开始DMA传输 */
        HAL_UART_Receive_DMA(&huart1, uart1_rx_data_t[uart1_buff_ctrl].buffer, UART1_BUFFER_SIZE);
    }
}

/* USER CODE END 0 */

/**
  * @brief  The application entry point.
  * @retval int
  */
int main(void)
{

  /* MCU Configuration--------------------------------------------------------*/

  /* Reset of all peripherals, Initializes the Flash interface and the Systick. */
  HAL_Init();

  /* Configure the system clock */
  SystemClock_Config();

  /* Initialize all configured peripherals */
  MX_GPIO_Init();
  MX_DMA_Init();
  MX_CAN1_Init();
  MX_I2C2_Init();
  MX_SPI1_Init();
  MX_TIM1_Init();
  MX_TIM2_Init();
  MX_UART4_Init();
  MX_UART5_Init();
  MX_USART1_UART_Init();
  MX_USART2_UART_Init();
  /* USER CODE BEGIN 2 */
	
	__HAL_UART_ENABLE_IT(&huart2, UART_IT_IDLE);    //使能串口中断
  HAL_UART_Receive_DMA(&huart2, uart2_rx_data_t[uart2_buff_ctrl].buffer, UART2_BUFFER_SIZE);    //使能串口DMA
	__HAL_UART_ENABLE_IT(&huart5, UART_IT_IDLE);
  HAL_UART_Receive_DMA(&huart5, uart5_rx_data_t[uart5_buff_ctrl].buffer, UART5_BUFFER_SIZE);
	
	__HAL_UART_ENABLE_IT(&huart1, UART_IT_IDLE);    //使能串口中断
  HAL_UART_Receive_DMA(&huart1, uart1_rx_data_t[uart1_buff_ctrl].buffer, UART1_BUFFER_SIZE);    //使能串口DMA
	
  /* USER CODE END 2 */

  /* Init scheduler */
  osKernelInitialize();

  /* Call init function for freertos objects (in cmsis_os2.c) */
  MX_FREERTOS_Init();

  /* Start scheduler */
  osKernelStart();

  /* We should never get here as control is now taken by the scheduler */

  /* Infinite loop */
  /* USER CODE BEGIN WHILE */
  while (1)
  {
    /* USER CODE END WHILE */

    /* USER CODE BEGIN 3 */
  }
  /* USER CODE END 3 */
}

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
/* USER CODE BEGIN 4 */
void HAL_CAN_RxFifo0MsgPendingCallback(CAN_HandleTypeDef *hcan)
{
    /* CAN1 接收中断 */
    if(hcan->Instance == CAN1)
    {
        CAN_RxHeaderTypeDef   Rx_Header;
        uint8_t data[8];
        if (HAL_CAN_GetRxMessage(&hcan1, CAN_RX_FIFO0,&Rx_Header, data) == HAL_OK)
        {
            Response_Handle(Rx_Header.ExtId,Rx_Header.StdId, data);
        }    
    }
}

/* USER CODE END 4 */

/**
  * @brief  Period elapsed callback in non blocking mode
  * @note   This function is called  when TIM4 interrupt took place, inside
  * HAL_TIM_IRQHandler(). It makes a direct call to HAL_IncTick() to increment
  * a global variable "uwTick" used as application time base.
  * @param  htim : TIM handle
  * @retval None
  */
void HAL_TIM_PeriodElapsedCallback(TIM_HandleTypeDef *htim)
{
  if (htim->Instance == TIM4) {
    HAL_IncTick();
  }
}

/**
  * @brief  This function is executed in case of error occurrence.
  * @retval None
  */
void Error_Handler(void)
{
  /* USER CODE BEGIN Error_Handler_Debug */
  /* User can add his own implementation to report the HAL error return state */
  __disable_irq();
  while (1)
  {
  }
  /* USER CODE END Error_Handler_Debug */
}

#ifdef  USE_FULL_ASSERT
/**
  * @brief  Reports the name of the source file and the source line number
  *         where the assert_param error has occurred.
  * @param  file: pointer to the source file name
  * @param  line: assert_param error line source number
  * @retval None
  */
void assert_failed(uint8_t *file, uint32_t line)
{
  /* USER CODE BEGIN 6 */
  /* User can add his own implementation to report the file name and line number,
     ex: printf("Wrong parameters value: file %s on line %d\r\n", file, line) */
  /* USER CODE END 6 */
}
#endif /* USE_FULL_ASSERT */

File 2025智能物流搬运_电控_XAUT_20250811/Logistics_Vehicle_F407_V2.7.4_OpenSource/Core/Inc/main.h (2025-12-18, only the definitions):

#define UART2_BUFFER_SIZE        (32)    //串口2缓冲区字节
#define UART5_BUFFER_SIZE        (16)    //串口5缓冲区字节
#define UART1_BUFFER_SIZE        (16)    //串口1缓冲区字节
#define UART3_BUFFER_SIZE        (16)    //串口3缓冲区字节
#define UART_BUFFER_QUANTITY     (5)
#define SPI2_RST_Pin GPIO_PIN_2
#define SPI2_RST_GPIO_Port GPIOE
#define SPI2_DC_Pin GPIO_PIN_3
#define SPI2_DC_GPIO_Port GPIOE
#define SPI2_CS_Pin GPIO_PIN_4
#define SPI2_CS_GPIO_Port GPIOE
#define BUZZER_Pin GPIO_PIN_0
#define BUZZER_GPIO_Port GPIOC
#define SPI2_MOSI_Pin GPIO_PIN_3
#define SPI2_MOSI_GPIO_Port GPIOC
#define SPI2_SCK_Pin GPIO_PIN_13
#define SPI2_SCK_GPIO_Port GPIOB
#define VM_SW_Pin GPIO_PIN_0
#define VM_SW_GPIO_Port GPIOD
#define Cam_Light_Pin GPIO_PIN_1
#define Cam_Light_GPIO_Port GPIOD
#define Start_Pin GPIO_PIN_3
#define Start_GPIO_Port GPIOD
#define SPI1_DC_Pin GPIO_PIN_4
#define SPI1_DC_GPIO_Port GPIOD
#define SPI1_CS_Pin GPIO_PIN_5
#define SPI1_CS_GPIO_Port GPIOD
#define SPI1_RST_Pin GPIO_PIN_6
#define SPI1_RST_GPIO_Port GPIOD
#define LED_3_Pin GPIO_PIN_3
#define LED_3_GPIO_Port GPIOB
#define LED_2_Pin GPIO_PIN_4
#define LED_2_GPIO_Port GPIOB
#define LED_1_Pin GPIO_PIN_5
#define LED_1_GPIO_Port GPIOB

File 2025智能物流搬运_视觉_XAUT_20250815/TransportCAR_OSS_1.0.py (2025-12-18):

# 2025年工创赛智能物流搬运赛道--西安理工大学塔吊结构--视觉部分开源
# 时间：2025/8/14 版本号：1.0

#这里是一些要下的库，大部分直接pip就能下下来
import cv2
import matplotlib as plt
import numpy as np
import serial as ser
import serial
import threading
import serial.tools.list_ports
from pyzbar.pyzbar import decode

# 从这里开始到93行都是卡尔曼滤波算法的初始化步骤
kalman = cv2.KalmanFilter(2, 2)
kalman_2 = cv2.KalmanFilter(2, 2)
kalman_3 = cv2.KalmanFilter(2, 2)

kalman.measurementMatrix = np.array([[1, 0], [0, 1]], np.float32)
kalman_2.measurementMatrix = np.array([[1, 0], [0, 1]], np.float32)
kalman_3.measurementMatrix = np.array([[1, 0], [0, 1]], np.float32)

kalman.transitionMatrix = np.array([[1, 0], [0, 1]], np.float32)
kalman_2.transitionMatrix = np.array([[1, 0], [0, 1]], np.float32)
kalman_3.transitionMatrix = np.array([[1, 0], [0, 1]], np.float32)

kalman.processNoiseCov = np.array([[1, 0], [0, 1]], np.float32) * 1e-3
kalman_2.processNoiseCov = np.array([[1, 0], [0, 1]], np.float32) * 1e-3
kalman_3.processNoiseCov = np.array([[1, 0], [0, 1]], np.float32) * 1e-3

kalman.measurementNoiseCov = np.array([[1, 0], [0, 1]], np.float32) * 0.01
kalman_2.measurementNoiseCov = np.array([[1, 0], [0, 1]], np.float32) * 0.01
kalman_3.measurementNoiseCov = np.array([[1, 0], [0, 1]], np.float32) * 0.01

kalman.statePre = np.array([[6], [6]], np.float32)
kalman_2.statePre = np.array([[6], [6]], np.float32)
kalman_3.statePre = np.array([[6], [6]], np.float32)

# 初始化变量
last_measurement = current_measurement = np.array((2, 2), np.float32)
last_prediction = current_prediction = np.array((2, 2), np.float32)

last_measurement_2 = current_measurement_2 = np.array((2, 2), np.float32)
last_prediction_2 = current_prediction_2 = np.array((2, 2), np.float32)

last_measurement_3 = current_measurement_3 = np.array((2, 2), np.float32)
last_prediction_3 = current_prediction_3 = np.array((2, 2), np.float32)


def kalman_filter(measured_value):
    global kalman, last_measurement, current_measurement, last_prediction, current_prediction

    last_measurement = current_measurement
    last_prediction = current_prediction

    # 更新测量值
    kalman.correct(measured_value)

    # 预测下一个状态
    current_prediction = kalman.predict()

    return current_prediction


def kalman_filter_2(measured_value):
    global kalman_2, last_measurement_2, current_measurement_2, last_prediction_2, current_prediction_2

    last_measurement_2 = current_measurement_2
    last_prediction_2 = current_prediction_2

    # 更新测量值
    kalman_2.correct(measured_value)

    # 预测下一个状态
    current_prediction_2 = kalman_2.predict()

    return current_prediction_2


def kalman_filter_3(measured_value):
    global kalman_3, last_measurement_3, current_measurement_3, last_prediction_3, current_prediction_3

    last_measurement_3 = current_measurement_3
    last_prediction_3 = current_prediction_3

    # 更新测量值
    kalman_3.correct(measured_value)

    # 预测下一个状态
    current_prediction_3 = kalman_3.predict()

    return current_prediction_3

# 定义串口接收和串口发送数组以及标志码unit任务码unit_target
receive = [0, 0, 0, 0]
send = [0x66, 0x00, 0x00, 0x00, 0x00, 0x00, 0x00, 0x00, 0x00, 0x00, 0x00, 0x00, 0x00, 0x00, 0x00]
unit = 0
unit_target = 1

fps = 0

# 创建串口进程函数
def uart_process():
    global receive  # receive the MCU's uart
    global number
    global unit  # mean the scenario of the map
    global unit_target  # mean the target of the scenario
    k = 0

    while True:
        input = ser.read(4)
        com_input = list(input)
        if com_input:  # 如果读取结果非空，则输出
            print(com_input)
            try:
                receive[0] = int(com_input[0])
                receive[1] = int(com_input[1])
                receive[2] = int(com_input[2])
                receive[3] = int(com_input[3])
            except:
                receive = [0, 0, 0, 0]
            print(receive)
            if (receive[0] == 102):
                unit = receive[1]
                unit_target = receive[2]
            else:
                None

# 由于在Jetson Nano中使用的串口设备是CH340所以这里直接设置为这个设备而不是COM口这里需要你们自己配置成自己的串口设备号
ser = serial.Serial(port="/dev/ttyCH341USB0", baudrate=115200, timeout=0.05)
#ser = serial.Serial(port="COM7" , baudrate=115200, timeout=0.05)
serial_thread = threading.Thread(target=uart_process)
serial_thread.daemon = True
serial_thread.start()

def color_blocks_position_WL (img,color,size_code):
    """
    根据命令借助HSV颜色阈值筛选识别指定的物料
    :param img: 输入的图像
    :param color: 要追踪的颜色目标对象（RGB）
    :param size_code: 颜色色块面积限幅（用于灵活筛选追踪颜色大小）
    :return: 相应色块的中心坐标
    """
    # 定义颜色识别阈值（HSV）
    color_dist = {'red': {'Lower1': np.array([156, 60, 60]), 'Upper1': np.array([180, 255, 255]),'Lower2': np.array([0, 60, 60]), 'Upper2': np.array([6, 255, 255])},
              'blue': {'Lower': np.array([100, 100, 45]), 'Upper': np.array([124, 255, 255])},
              'green': {'Lower': np.array([38, 80, 45]), 'Upper': np.array([90, 255, 255])},
              }
    ball_color = color
    if img is not None:
        gs_img = cv2.GaussianBlur(img, (5, 5), 0)                     # 高斯模糊
        hsv_img = cv2.cvtColor(gs_img, cv2.COLOR_BGR2HSV)                 # 转化成HSV图像
        erode_hsv = cv2.erode(hsv_img, None, iterations=2)                   # 腐蚀 粗的变细（平整边缘）
        inRange_hsv = None
        # 红色在HSV空间阈值有两部分所以需要特殊处理
        if (ball_color == 'red'):
            inRange_hsv1 = cv2.inRange(erode_hsv, color_dist[ball_color]['Lower1'], color_dist[ball_color]['Upper1'])
            res1 = cv2.bitwise_and(erode_hsv, erode_hsv, mask=inRange_hsv1)
            inRange_hsv2 = cv2.inRange(erode_hsv, color_dist[ball_color]['Lower2'], color_dist[ball_color]['Upper2'])
            res2 = cv2.bitwise_and(erode_hsv, erode_hsv, mask=inRange_hsv2)
            inRange_hsv = inRange_hsv1 + inRange_hsv2
        else:
            inRange_hsv = cv2.inRange(erode_hsv, color_dist[ball_color]['Lower'], color_dist[ball_color]['Upper'])
        cv2.imshow("end2",erode_hsv)
        cv2.imshow("end",inRange_hsv)
        cnts = cv2.findContours(inRange_hsv.copy(), cv2.RETR_EXTERNAL, cv2.CHAIN_APPROX_SIMPLE)[-2]# 找角点
        c = max(cnts, key=cv2.contourArea)# 筛选面积最大的色块
        size = int(cv2.contourArea(c))
        print(size)
        if (size > size_code): # 面积限幅
            rect = cv2.minAreaRect(c)
            box = cv2.boxPoints(rect)
            cv2.drawContours(img0, [np.int0(box)], -1, (0, 255, 255), 2)
            center_x, center_y = rect[0]
            return (int(center_x), int(center_y)) # 返回相应色块的中心坐标
        else:
            pass
    else:
        print("无画面")
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

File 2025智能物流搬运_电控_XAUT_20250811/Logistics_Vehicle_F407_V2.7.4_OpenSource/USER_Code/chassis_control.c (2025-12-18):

/**
  ******************************************************************************
  * @author  PINK SAKURA
  * @version V1.0
  * @date    2024-08-08
  * @brief   底盘控制 C 文件
  ******************************************************************************
  * @attention
  * 邮箱：sakura.mail@qq.com
  ******************************************************************************
  */

#include "chassis_control.h"

float rcKpx	= 8, rcKpy = 8, rcKpz = 6;       //move函数Kp
float mKpx	= 2.3, mKpy = 2.3, mKpz = 9;     //move函数Kp
float vKpx	= 1.2, vKpy =1.2, vKpz = 2.4;    //调整函数Kp
float cvKpz	= 0.08;    //z轴调整函数Kp
int last_Speed[4]={0};

float XYVmax;
float ZVmax;
float XYVmin;
float ZVmin;

uint8_t in_pos = 1;      //就位指示
uint8_t v_in_pos = 1;    //视觉就位指示
uint8_t near_pos = 1;    //接近指示
uint8_t delay_pos=0;
uint8_t delay_turn=0;
uint8_t delay_visual=0;
	
	float devx=0;
	float devy=0;
	float devz=0;

void SpeedTarget_stop(void)  //电机停转
{
	SpeedTarget[0]=0;
	SpeedTarget[1]=0;
	SpeedTarget[2]=0;
	SpeedTarget[3]=0;
}

//-------------------------------------------------------------------------------------------------------------------
//  @brief      		 电机转速和方向控制函数
//  @return     		 /
//  @param					 int MotorSpeed1  电机1目标速度
//  @param					 int MotorSpeed2  电机2目标速度
//  @param					 int MotorSpeed3  电机3目标速度
//  @param					 int MotorSpeed4  电机4目标速度
//  @Sample usage:   略
//-------------------------------------------------------------------------------------------------------------------
void SetMotorVoltageAndDirection(int MotorSpeed1, int MotorSpeed2, int MotorSpeed3, int MotorSpeed4)  //电机转速和方向控制函数
{
  uint8_t MCommand1[8]={0x01,0xF6,0x00,0x00,0x10,0x00,0x00,0x6B};  //定义电机控制命令
	uint8_t MCommand2[8]={0x02,0xF6,0x00,0x00,0x10,0x00,0x00,0x6B};
	uint8_t MCommand3[8]={0x03,0xF6,0x00,0x00,0x10,0x00,0x00,0x6B};
	uint8_t MCommand4[8]={0x04,0xF6,0x00,0x00,0x10,0x00,0x00,0x6B};
	
	if (MotorSpeed1<0) {MotorSpeed1=-MotorSpeed1; MCommand1[2]=0x01;}  //电机方向指令
	MCommand1[3]=(MotorSpeed1 >> 8); MCommand1[4]=(MotorSpeed1 >> 0);  //电机速度指令
	
	if (MotorSpeed2<0) {MotorSpeed2=-MotorSpeed2; MCommand2[2]=0x01;}
	MCommand2[3]=(MotorSpeed2 >> 8); MCommand2[4]=(MotorSpeed2 >> 0); 
	
	if (MotorSpeed3<0) {MotorSpeed3=-MotorSpeed3; MCommand3[2]=0x01;}
	MCommand3[3]=(MotorSpeed3 >> 8); MCommand3[4]=(MotorSpeed3 >> 0); 
	
	if (MotorSpeed4<0) {MotorSpeed4=-MotorSpeed4; MCommand4[2]=0x01;}
	MCommand4[3]=(MotorSpeed4 >> 8); MCommand4[4]=(MotorSpeed4 >> 0); 
	
  HAL_UART_Transmit(&huart4,(uint8_t *)MCommand1,8,HAL_MAX_DELAY);   //指令发送
	  osDelay(1);
  HAL_UART_Transmit(&huart4,(uint8_t *)MCommand2,8,HAL_MAX_DELAY);
  	osDelay(1);
  HAL_UART_Transmit(&huart4,(uint8_t *)MCommand3,8,HAL_MAX_DELAY);
  	osDelay(1);
  HAL_UART_Transmit(&huart4,(uint8_t *)MCommand4,8,HAL_MAX_DELAY);
}

//-------------------------------------------------------------------------------------------------------------------
//  @brief      		 速度用限幅
//  @return     		 /
//  @param					 float* value  输入值指针
//  @param					 float max     最大值
//  @param					 float min     最小值
//  @param					 float dead_zone     死区/不响应区域（防止抖动）
//  @Sample usage:   略
//-------------------------------------------------------------------------------------------------------------------
void numerical_limit(float* value, float max, float min , float dead_zone)
{
	if (*value > dead_zone)
		*value += min;
	else if (*value < -dead_zone)
	  *value -= min;
	if (*value > max)
		*value = max;
	else if (*value <- max)
	  *value = -max;
}

//-------------------------------------------------------------------------------------------------------------------
//  @brief      		 底盘遥控函数
//  @return     		 /
//  @param					 short x  X轴速度
//  @param					 short y  Y轴速度
//  @param					 short z  Z轴速度
//  @Sample usage:   略
//-------------------------------------------------------------------------------------------------------------------
void chassis_RC(short x,short y,short z)      //底盘遥控函数
{
  XYVmax=800;
	ZVmax=600;
	
//	  float length = sqrt( x * x + y * y );      //归一化处理
//       x = ( x / length ) * 100;
//       y = ( y / length ) * 100;

		int Speed[4]={0};
		devx = x;
		devy = y;
		devz = z;
		
		float vx1 = 0,vy1 = 0,vz = 0;

		vx1 =1 * rcKpx * devx;
		numerical_limit(&vx1, XYVmax, 0, 5);
			
		vy1 =1 * rcKpy * devy;
		numerical_limit(&vy1, XYVmax, 0, 5);

		vz = rcKpz * devz;
		numerical_limit(&vz, ZVmax, 0, 5);

		float v_ratio = 1;
			
    Speed[0] =   ( ( vy1 + vx1 ) * v_ratio + vz);
  	Speed[1] = - ( ( vy1 - vx1 ) * v_ratio - vz);
  	Speed[2] =   ( ( vy1 - vx1 ) * v_ratio + vz);
  	Speed[3] = - ( ( vy1 + vx1 ) * v_ratio - vz);

    for(uint8_t i=0;i<4;i++)       //速度提交
	  {
			SpeedTarget[i]=(int)(Speed[i] * 0.238);
	  }
}

//-------------------------------------------------------------------------------------------------------------------
//  @brief      		 底盘定位系统位置环
//  @return     		 /
//  @param					 int x  X轴目标位置
//  @param					 int y  Y轴目标位置
//  @param					 int z  Z轴目标位置
//  @Sample usage:   略
//-------------------------------------------------------------------------------------------------------------------
void chassis_move(int x,int y,int z)      //底盘移动函数
{
  XYVmax=1600;
	ZVmax=750;
	XYVmin=5;
	ZVmin=5;

		int Speed[4]={0};
	  devx=pos_x-x;
	  devy=pos_y-y;
	  if(z*zangle<0&&abs(z)+fabs(zangle)>180)
      devz=-(360-abs(z)-fabs(zangle));
		else 
      devz=z-zangle;
		
		float vx1 = 0,vy1 = 0,vx2 = 0,vy2 = 0,vz = 0;
		
		vy1 =cos(zangle*3.141f/180) * mKpy * devy;
		vx2 =sin(zangle*3.141f/180) * mKpy * devy;
		numerical_limit(&vy1, XYVmax, XYVmin, 5);
		numerical_limit(&vx2, XYVmax, XYVmin, 5);
			
		vy2 =sin(zangle*3.141f/180) * mKpx * devx;
		vx1 =cos(zangle*3.141f/180) * mKpx * devx;
		numerical_limit(&vy2, XYVmax, XYVmin, 5);
		numerical_limit(&vx1, XYVmax, XYVmin, 5);

		vz = mKpz * devz;
    numerical_limit(&vz, ZVmax, 0, 5);
	
    Speed[0] = - (  vy1  -vy2  +  vx1  +vx2  +  vz);
  	Speed[1] =   (  vy1  -vy2  -  vx1  -vx2  -  vz);
  	Speed[2] = - (  vy1  -vy2  -  vx1  -vx2  +  vz);
  	Speed[3] =   (  vy1  -vy2  +  vx1  +vx2  -  vz);

    for(uint8_t i=0;i<4;i++)       //速度提交
	  {
			if (Speed[i]>0&&Speed[i]>last_Speed[i])
				Speed[i]=last_Speed[i]+20;
			if (Speed[i]<0&&Speed[i]<last_Speed[i])
				Speed[i]=last_Speed[i]-20;
			SpeedTarget[i]=(int)(Speed[i] * 0.238);
			last_Speed[i]=Speed[i];
	  }
		if((devx<100&&devx>-100)&&(devy<100&&devy>-100)&&(devz<30&&devz>-30))
			near_pos = 1;
    if((devx<60&&devx>-60)&&(devy<60&&devy>-60)&&(devz<15&&devz>-15))
			delay_pos++;
		else
			delay_pos=0;
		
		if (delay_pos>10)
			in_pos = 1;
}
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

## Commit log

2025-12-18 附加资料及参数提交
    [2025智能物流搬运_物料清单_XAUT_20250927.xlsx, 2025智能物流搬运_通讯协议_XAUT_20250811.xlsx]
2025-12-18 工程文件提交
    [2.DWG, 2025-场地.SLDPRT, 2025-物料.SLDPRT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]
2025-12-18 说明文件更新
2025-12-18 项目简介及任务命题文档
2025-12-18 许可证更新
2025-12-18 Readme更新
2026-05-19 修改了PCB的错误器件参数

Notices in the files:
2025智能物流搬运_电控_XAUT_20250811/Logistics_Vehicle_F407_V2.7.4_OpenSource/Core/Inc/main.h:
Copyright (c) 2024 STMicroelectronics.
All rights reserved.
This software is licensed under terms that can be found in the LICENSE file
